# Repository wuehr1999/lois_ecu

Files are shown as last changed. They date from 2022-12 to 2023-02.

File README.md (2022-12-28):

# lois_ecu
This repository contains the [hardware](https://github.com/wuehr1999/lois_ecu/tree/main/hw), [firmware](https://github.com/wuehr1999/lois_ecu/tree/main/firmware) and [tooling](https://github.com/wuehr1999/lois_ecu/tree/main/rpmctrl_tuning) for a general purpose control unit for differential drive based wheeled robotics platforms. An image of the real hardware and a component diagram are shown below.
<p align="center">
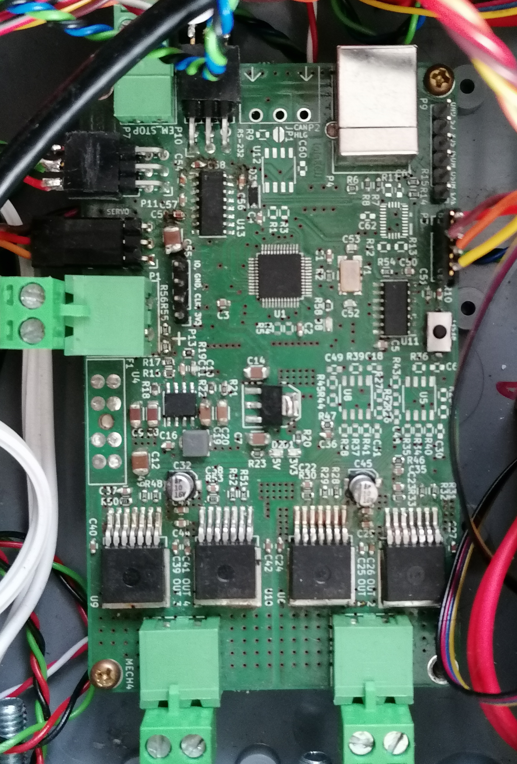
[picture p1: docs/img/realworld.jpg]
  
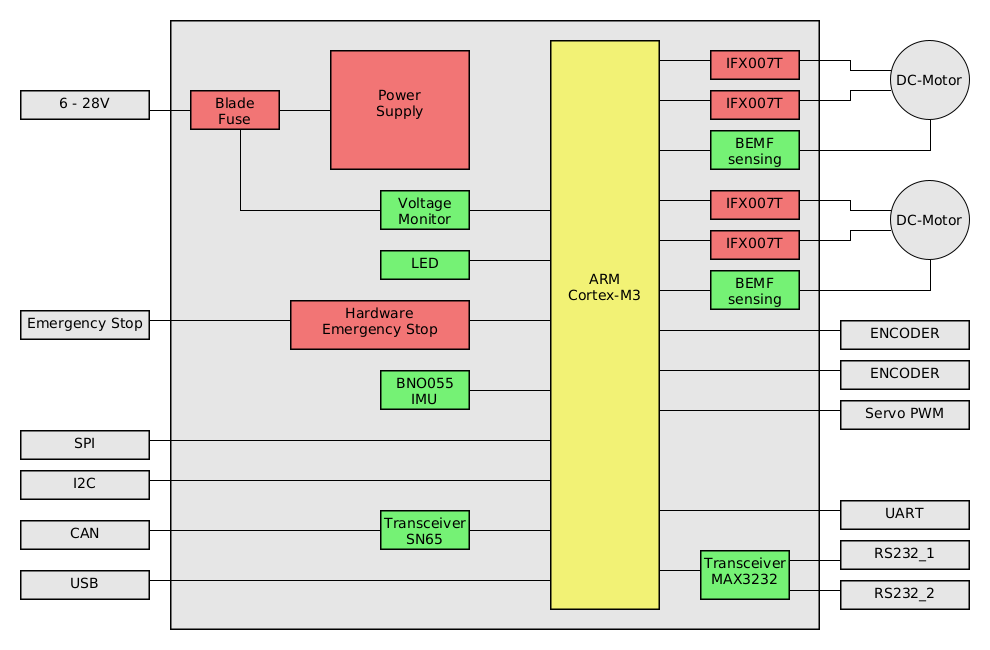
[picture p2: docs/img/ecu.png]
  
</p>

## Firmware

The [firmware](https://github.com/wuehr1999/lois_ecu/tree/main/firmware/loisECU) comes as a STM32 CubeIDE project and currently implements the following features:

- Closed single loop RPM-control for two DC-motors with encoders
- Realtime calculation of differential drive odometry
- Servo sweep for the [ball distribution device](https://github.com/generationmake/BDD)
- NMEA parser on RS232_1 (used for UBLOX GPS)
- NMEA parser on RS232_2 (used for KVH-C100 fluxgate compass)
- Host communication via UART
- 2048 Byte reealtime reord buffer ( recording of RPM, torque and compass heading over a given time )
- Easy human readable and debuggable ASCII communication leaned on modbus protocol with optional checksum

### Host communication protocol

The communication protocol is ASCII-based and the messages have the following format:

```:<8-bit command><32-bit payload><8-bit crc><\n>```

All values are written in hexadecimal, so that every message has a fixed length of 14 characters. There is also a [ROS2 driver](https://github.com/wuehr1999/lois_ecu_ros), which uses the given protocol to make the functionalities available via ROS.

The table below shows the currently implemented messages. There are also some periodic messages from the ECU to the Host. By writing the commands of this messages to the ECU, the period can be changed. The payload is then interpreted as an ```uint16``` containing the period time in milliseconds. ```0xfffe``` then means requesting a periodic message once and ```0xffff``` turns the message off completely.

| Command | Function | To ECU (E)/ To Host (H) | Payload interpretation | Periodic |
| - | - | - | - | - |
| ```0x01``` | Dutycycle of left and right motor, RPM controller gets disabled | E | ```2 x int16``` ( -100 % - 100 %)  | |
| ```0x02``` | RPM of left and right motor, RPM controller gets enabled | E | ```2 x int16``` | |
| ```0x03```  | Turn board LED on or off | E | ```bool``` | |
| ```0x04``` | Record a given amount of RPM samples | E / H | ```2 x uint16``` ( m samples left and n right ) to ECU or sequential max(m, n) ``` 2 x uint16``` ( tick timestamps in 100 ns followed by ```0x00000000``` ) to Host |  |
| ```0x05``` | Emergency stop button pressed | H | ```bool``` |  |
| ```0x06``` | Kp left controller | E | ```float32``` |  |
| ```0x07``` | Tn left controller | E | ```float32``` |  |
| ```0x08``` | Td left controller | E | ```float32``` |  |
| ```0x09``` | Kp right controller | E | ```float32``` |  |
| ```0x0a``` | Tn right controller | E | ```float32``` |  |
| ```0x0b``` | Td right controller | E | ```float32``` |  |
| ```0x0c``` | Record a given amount of compass heading samples | E | ```uint32```  n samples to ECU or sequential n + 1 ```2 x int16``` ( heading data in degrees ) followed by ```0x016A016A``` to Host |  |
| ```0x0d``` | GPS position | E / H | 3 sequential ```uint32, 2 x float32``` ( ```0xffffffff```, latitude, longitude ) | x |
| ```0x0e``` | GPS time | E / H | ```3 x uint8``` ( hours, minutes, seconds ) | x |
| ```0x0f``` | GPS date | E / H | ```3 x uint8``` ( year, month, day ) | x |
| ```0x10``` | Compass heading | E / H | ```1 x int16``` ( degrees to north ) | x |
| ```0x11``` | Terminal mode ( forward serial sensor Rx input on this interface ) | E | ```uint8``` ( Host protocol, GPS sensor, compass sensor ) | |
| ```0x12``` | Encoder overall ticks | E / H | 4 sequential ```4 x uint32``` ( ```0xffffffff```, timestamp in nanoseconds, left encoder, right encoder )  | x |
| ```0x13``` | Left encoder short level time correction | E | ```float32``` |  |
| ```0x14``` | Left encoder long level time correction | E | ```float32``` |  |
| ```0x15``` | Right encoder short level time correction | E | ```float32``` |  |
| ```0x16``` | Right encoder long level time correction | E | ```float32``` |  |
| ```0x17``` | Record a given amount of Torque samples | E / H | ```2 x uint16``` ( m samples left and n right ) to ECU or sequential max(m, n) ``` 2 x uint16``` ( torque 12-bit ADC values followed by ```0x00000000``` ) to Host |  |
| ```0x18``` | Reset all controllers, interfaces and counters | E  | - |  |
| ```0x19``` | Use ball distribution device once | E | - |  |
| ```0x20``` | Odometry calculated on robot | E / H | sequential 7 started with ```0xffffffff``` followed by ```6 x float32``` ( x, y, phi, dx, dy, dphi ) | x |

## Encoder and RPM controller tuning

There is [tooling in Scilab](https://github.com/wuehr1999/lois_ecu/tree/main/rpmctrl_tuning) provided, that can be used to find the parameters for the implemented RPM controller. The first step is recording a step response with full torque/ dutycycle and data of free spinning wheels at a constant dutycycle and  saving the data as ```*.csv``` files. This can for instance be done by using the ROS ecosystem of lois. There are also some examples in the controller tuning folder.

### Encoder correction

The ECU determines the RPM values of the robot by measuring the time of high and low levels of the encoder signals. With this implementation, also encoders with fewer steps ( usually mounted directly on the wheel ) can be used with a sufficient resolution. The problem is, that some encoders have inequal high and low times. Therefore [correction factors](https://github.com/wuehr1999/lois_ecu/blob/main/rpmctrl_tuning/edgecorrect/correct.sce) can be calculated and entered at runtime ( commands ```0x13 - 0x16``` ) from the free spinning record.

### Finding the controller parameters

The controller is updated in the ECU with a frequency of ```5 Hz```. It is only a single loop RPM controller without a cascade for torque control, as it is not necessary for most differential drivetrain applications.

There is one band limited PI controller for each motor with the transfer function ```G(s) = Kp * ( 1 + s * Tn ) / ( s * Tn * ( 1 + s * Td ))```.

The Scilab tooling helps to [approximate the plant from the step response as 1st or 2nd order system and find sufficient controller settings](https://github.com/wuehr1999/lois_ecu/blob/main/rpmctrl_tuning/stepresponse/main.sce). The tuning paradigm is the compensation of the most critical pole of the plant followed by gain optimization. The following [goal parameters](https://github.com/wuehr1999/lois_ecu/blob/main/rpmctrl_tuning/stepresponse/init.sce) that can be selected:
- Encoder steps per revolution
- Controller frequency in Hz
- Don't optimize for phase margin with gain optimum ( ```Td = 0``` )
- Maximum overshoot inpercent
- Step response destination in % for optimization ( average RPM value during operation )
- Stabilization time in seconds
- Tolerance band in %

## PCB toplayer

<p align="center">
  <img src=docs/img/toplayer.png width="75%">
</p>

## PCB bottomlayer

<p align="center">
  <img src=docs/img/bottomlayer.png width="75%">
</p>

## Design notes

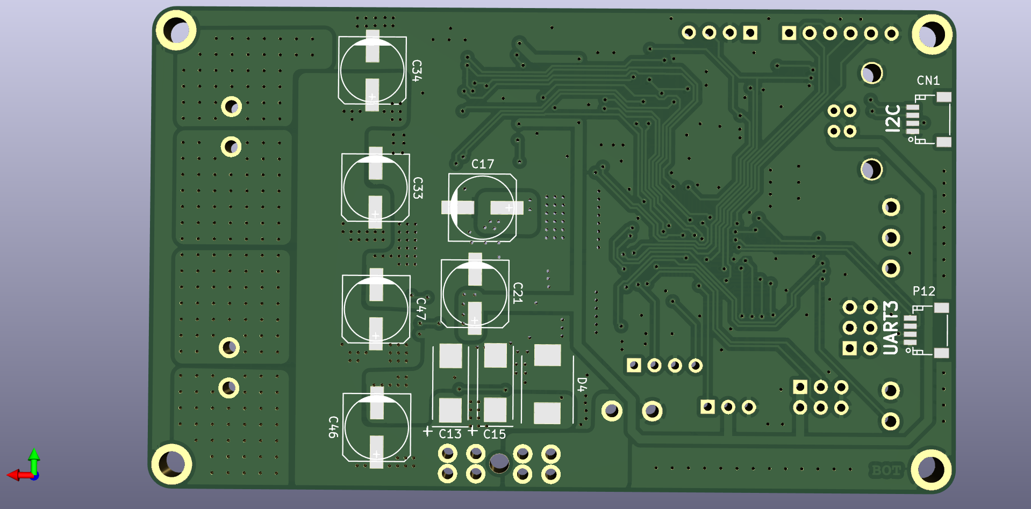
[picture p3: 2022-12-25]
docs/img/bottomlayer.png

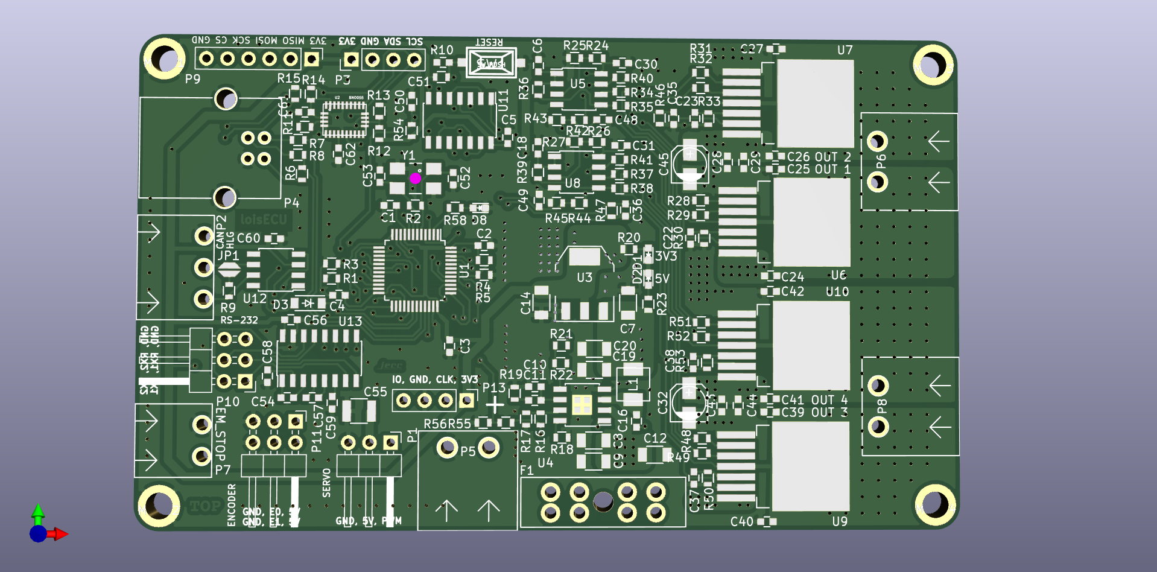
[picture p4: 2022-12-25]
docs/img/toplayer.png

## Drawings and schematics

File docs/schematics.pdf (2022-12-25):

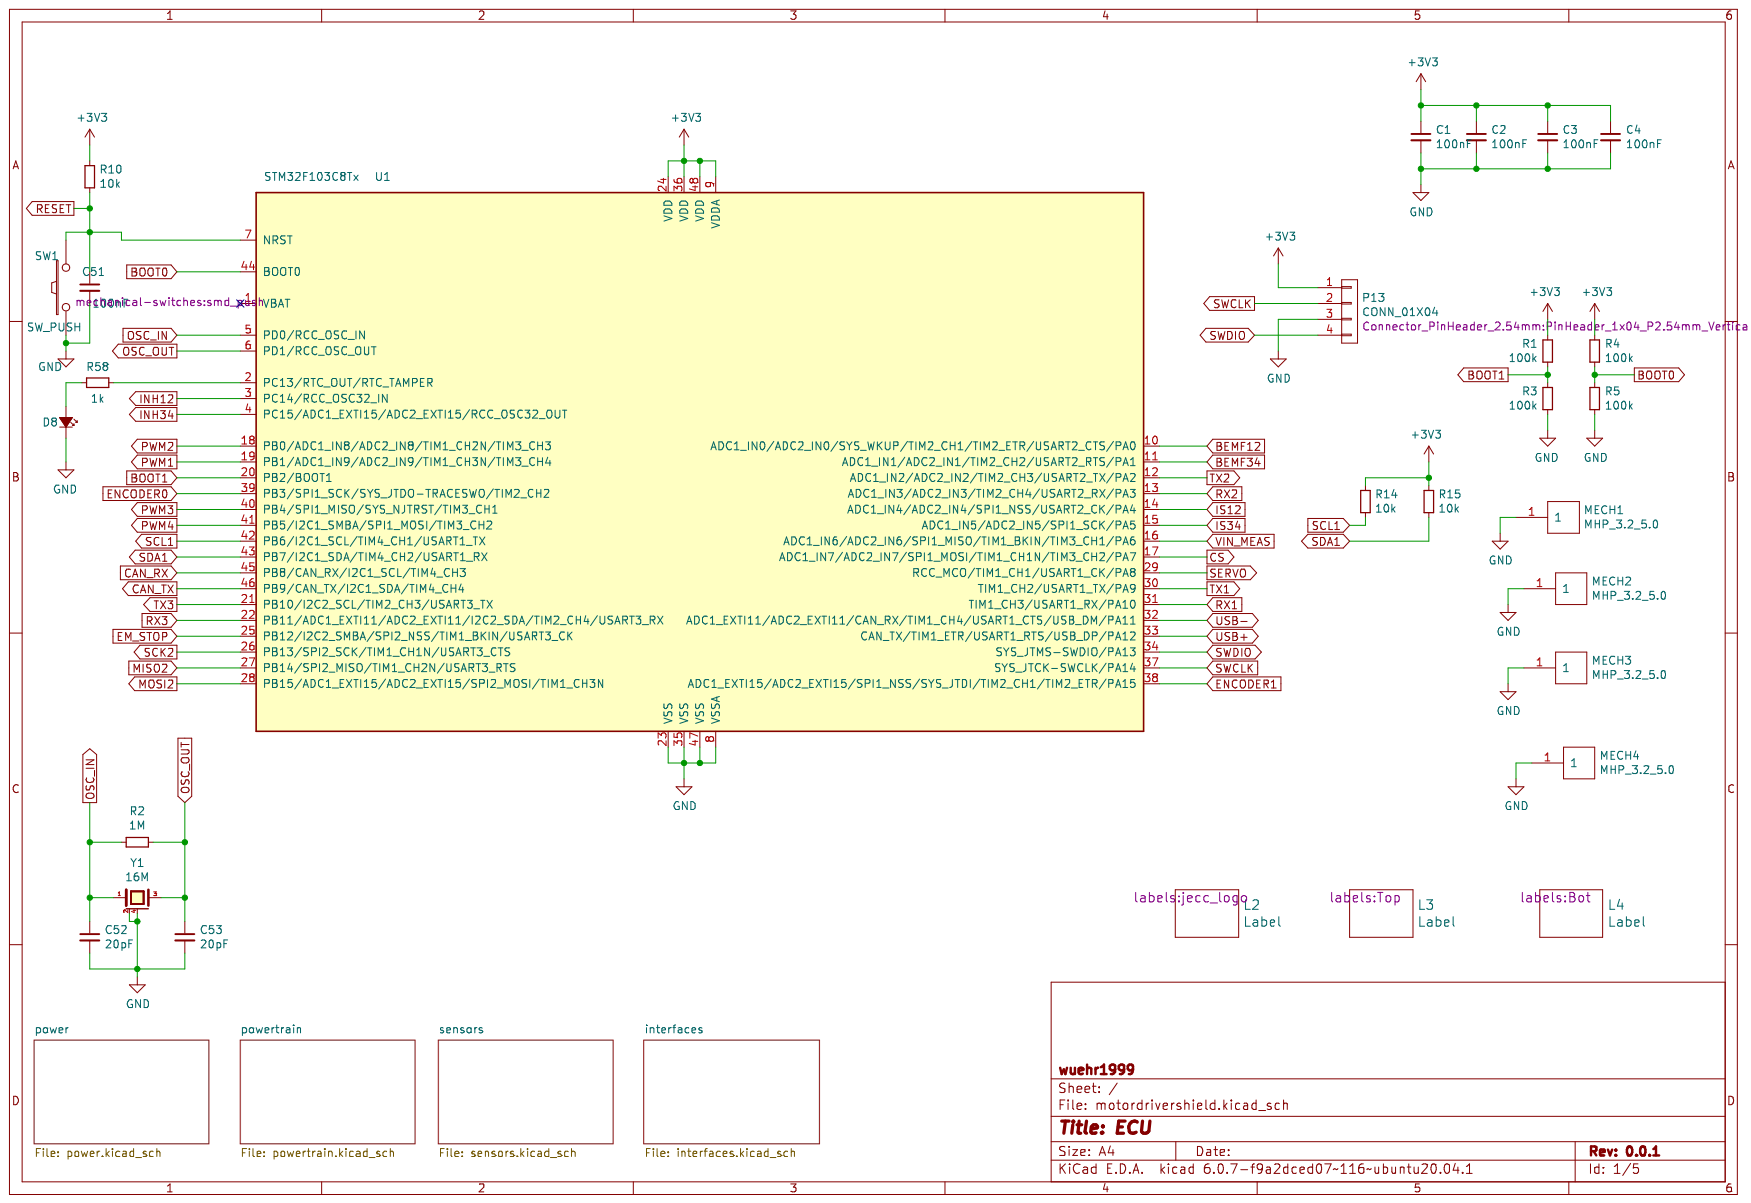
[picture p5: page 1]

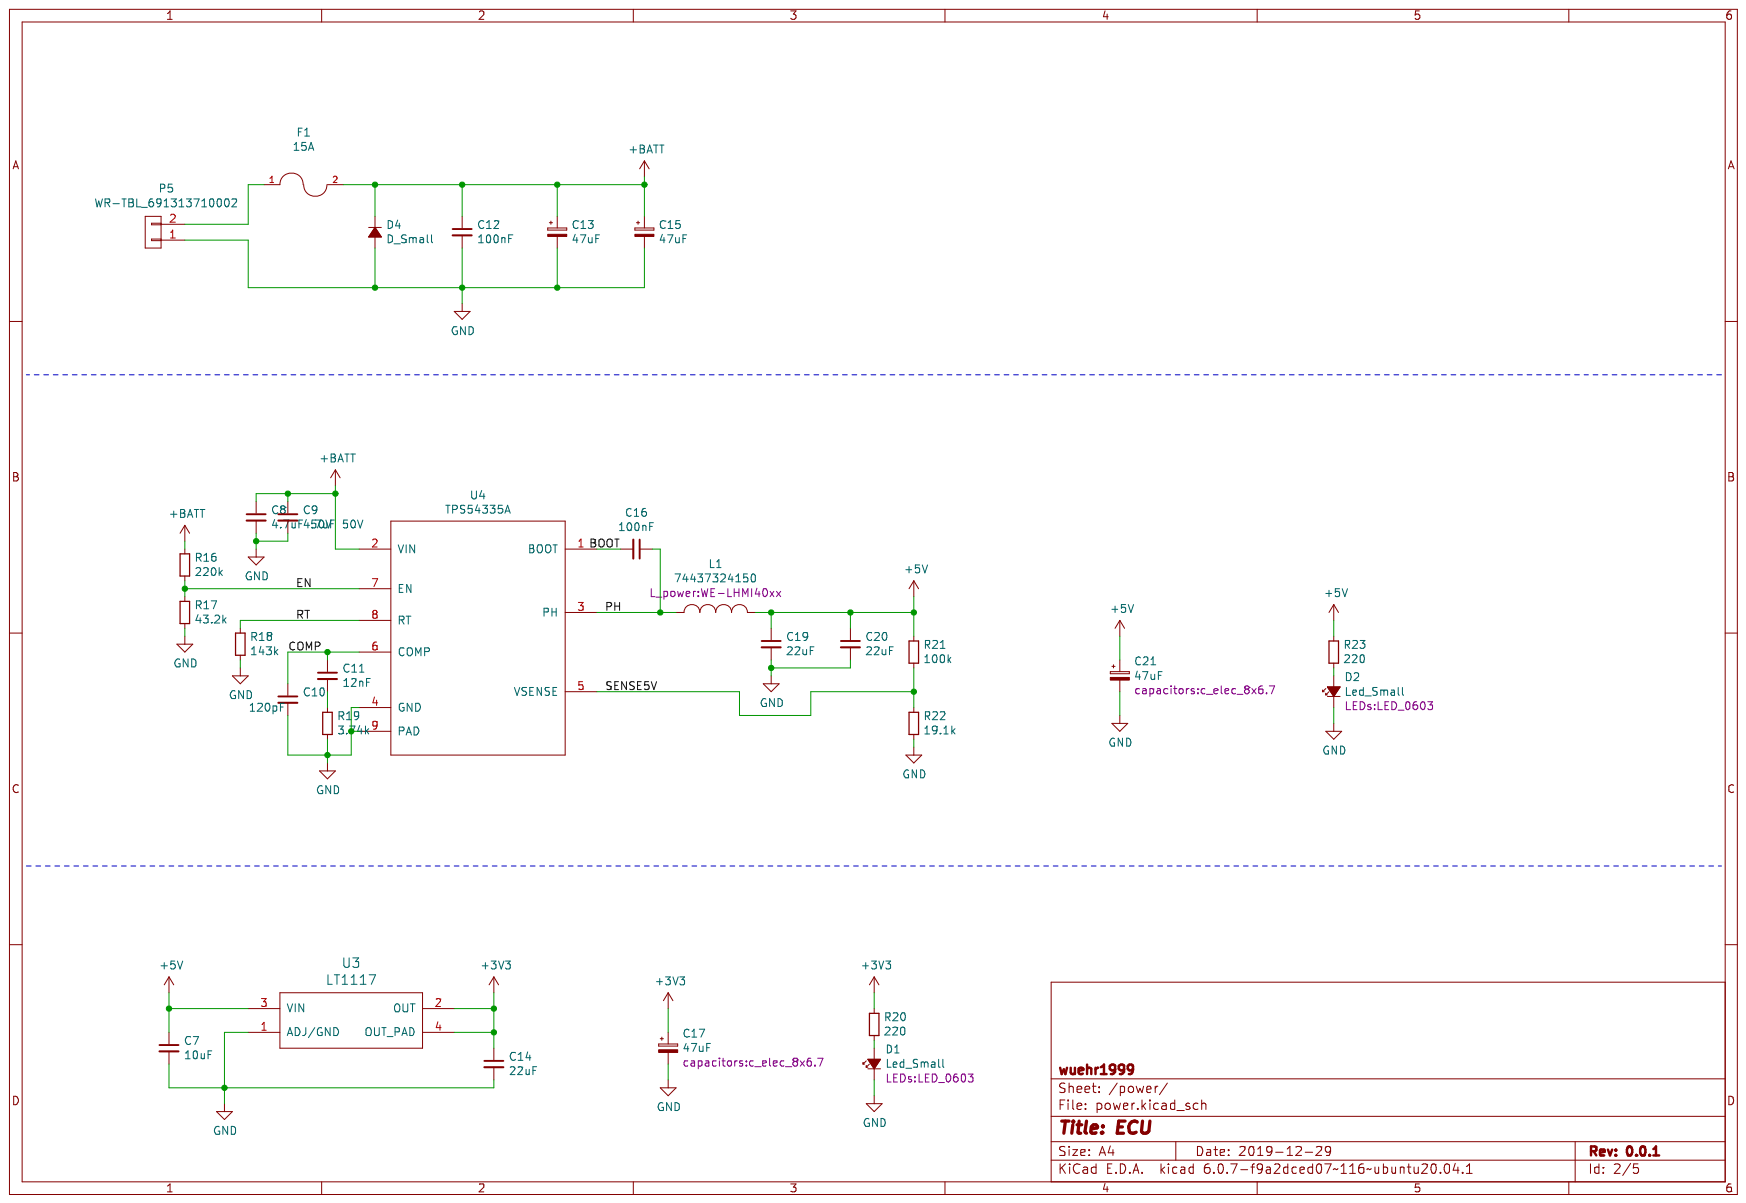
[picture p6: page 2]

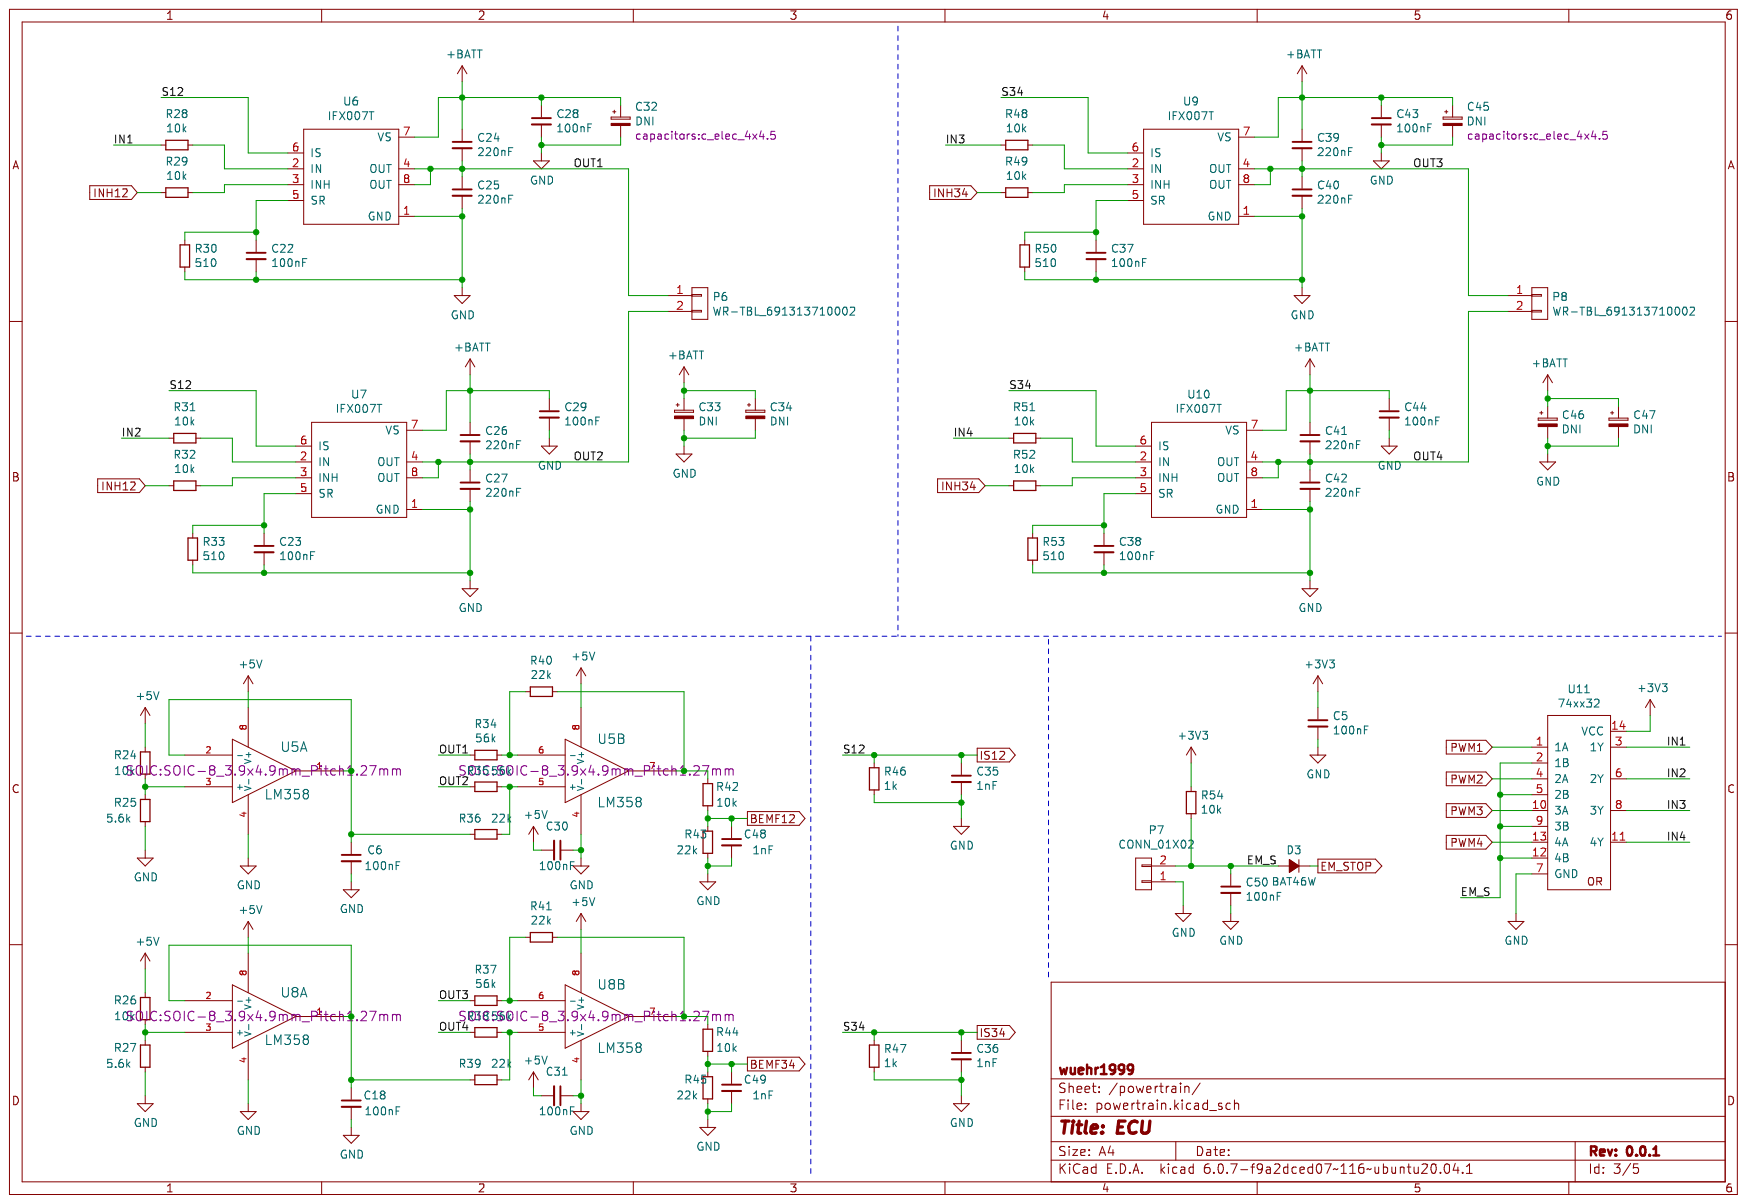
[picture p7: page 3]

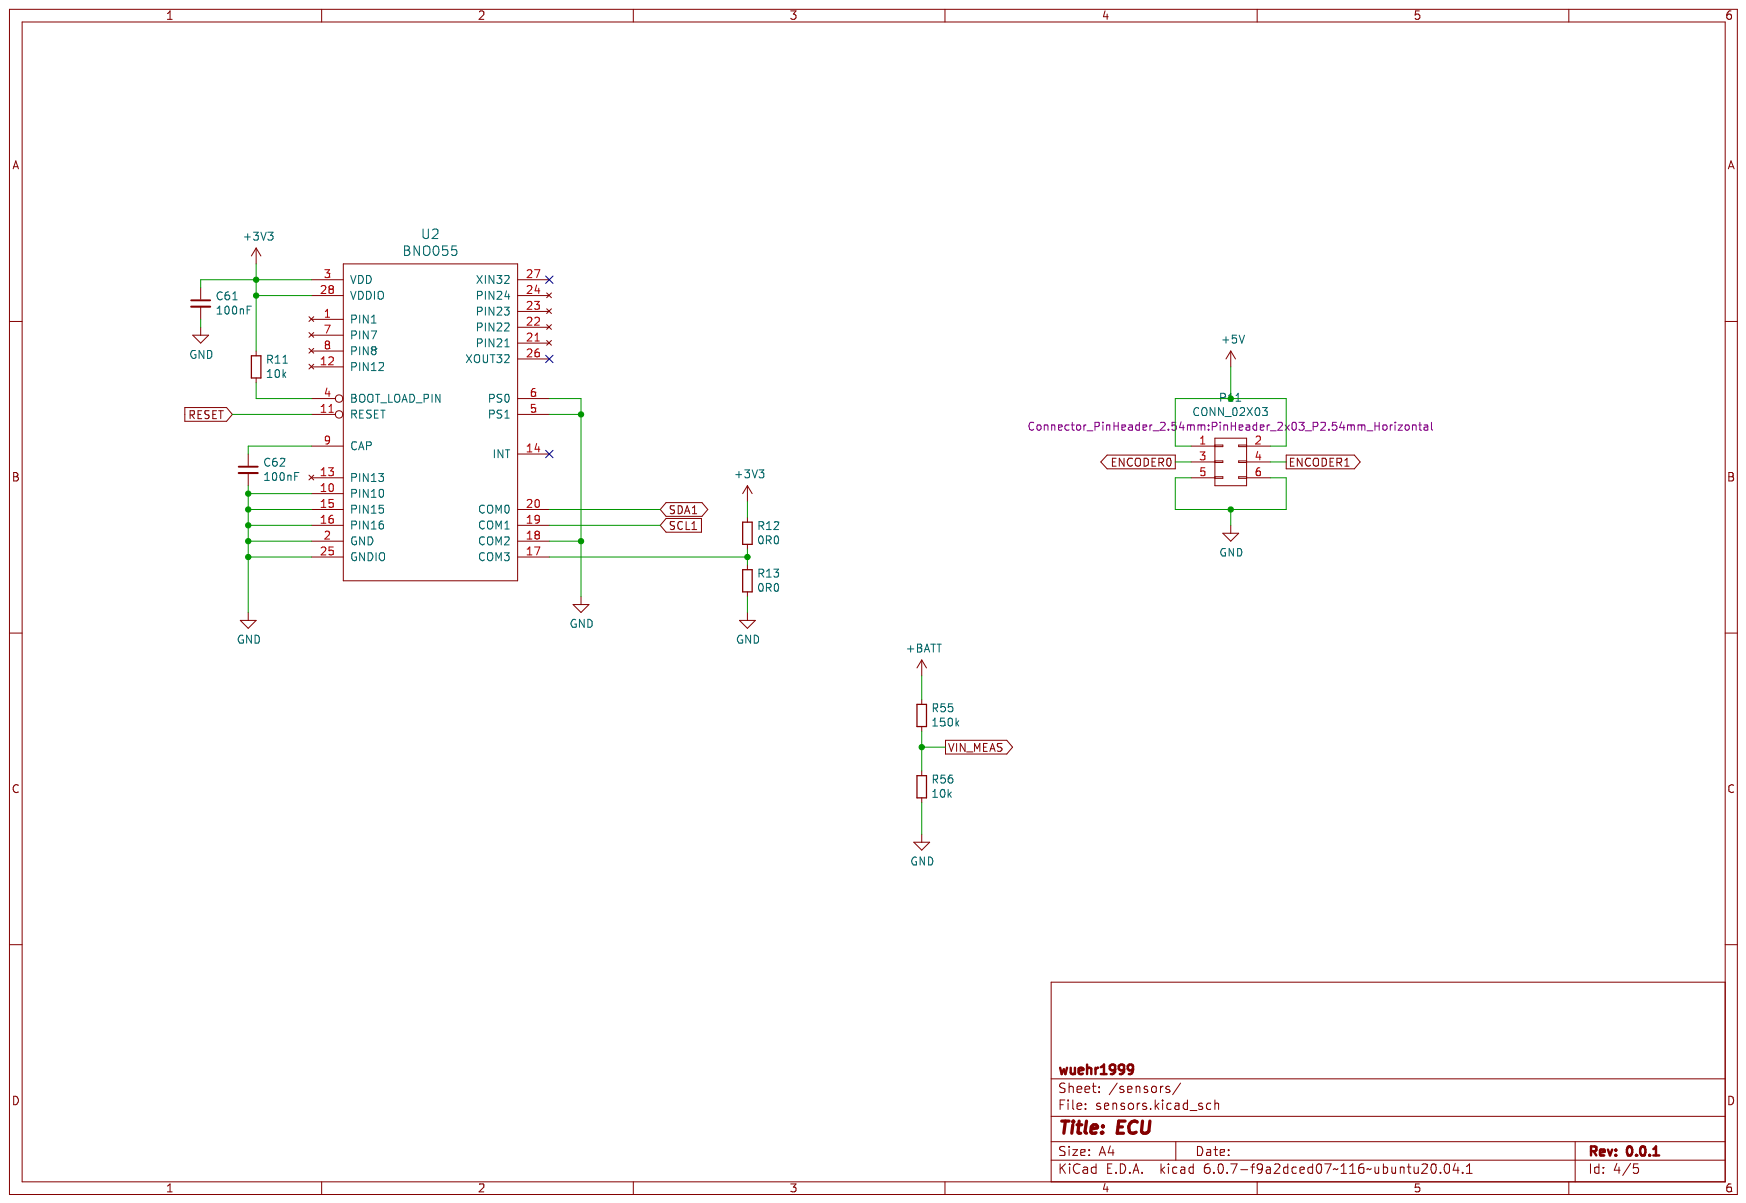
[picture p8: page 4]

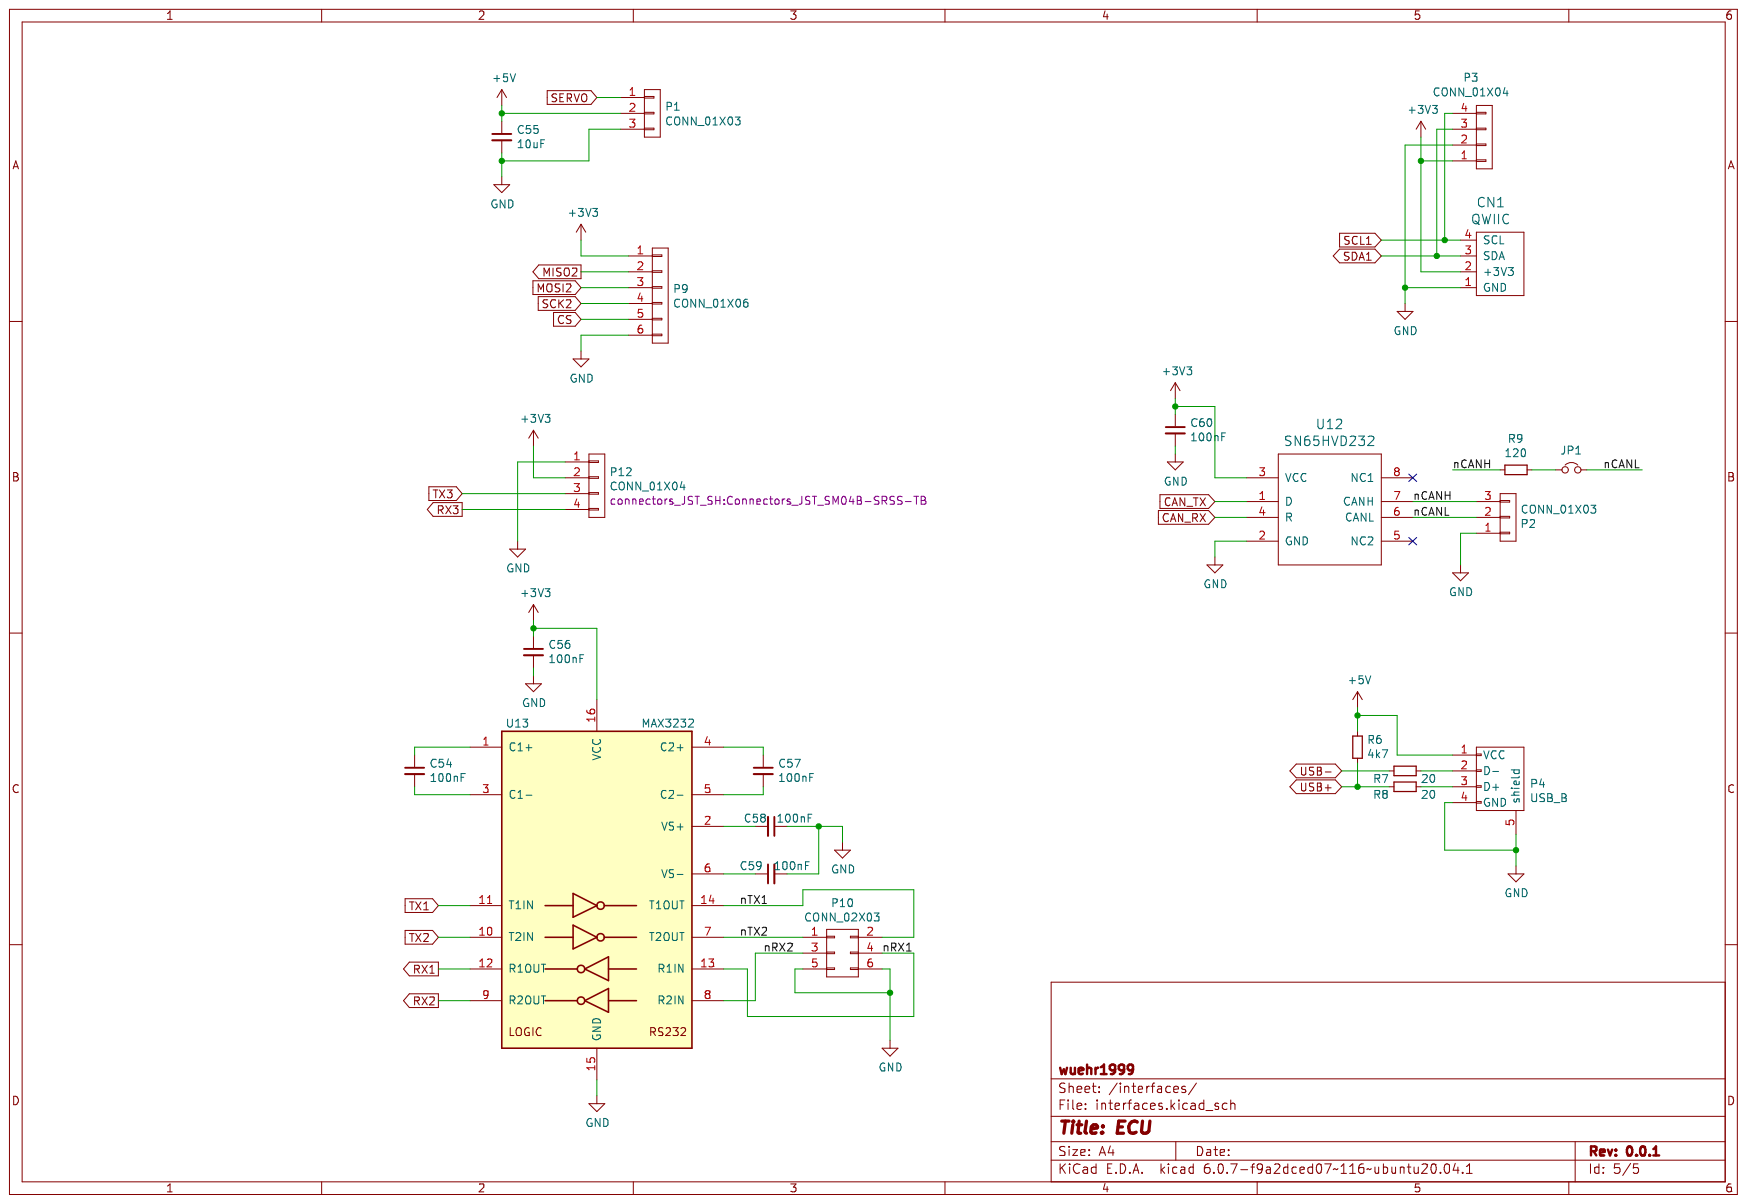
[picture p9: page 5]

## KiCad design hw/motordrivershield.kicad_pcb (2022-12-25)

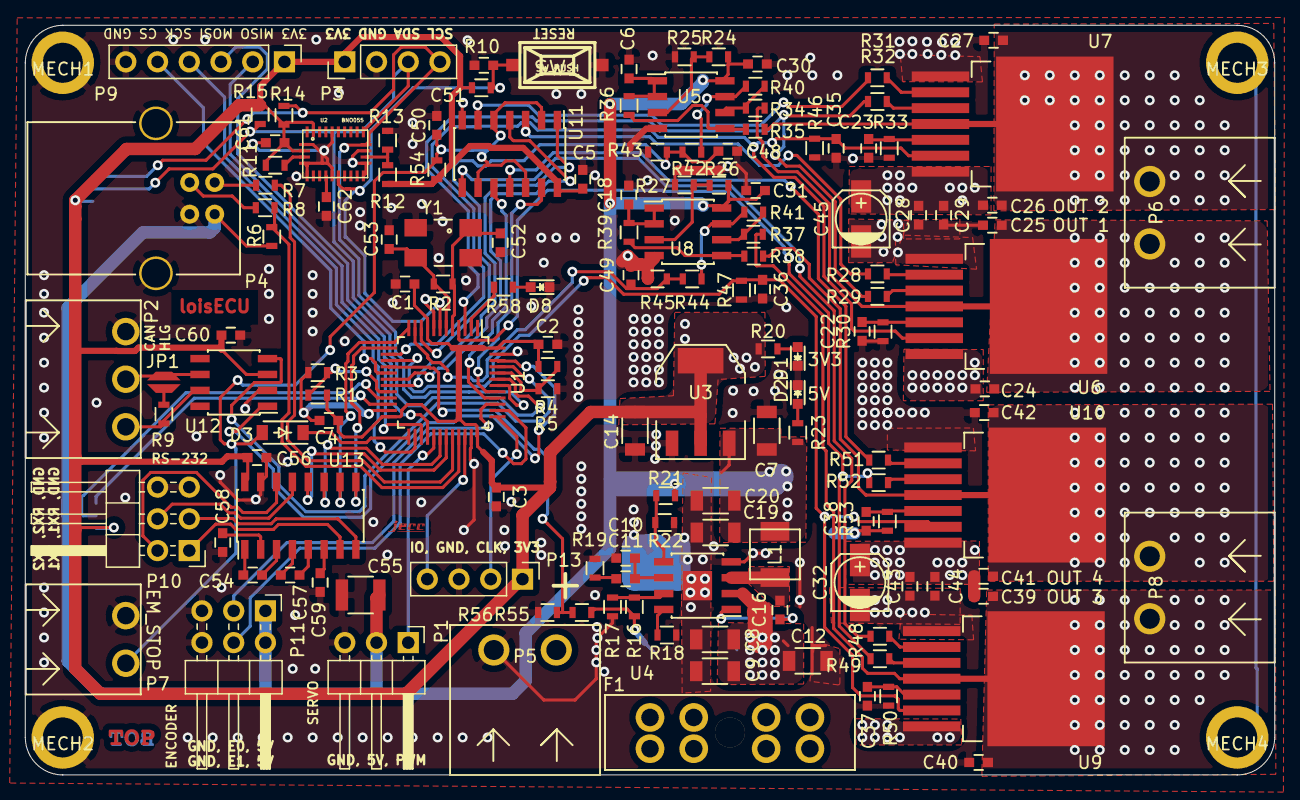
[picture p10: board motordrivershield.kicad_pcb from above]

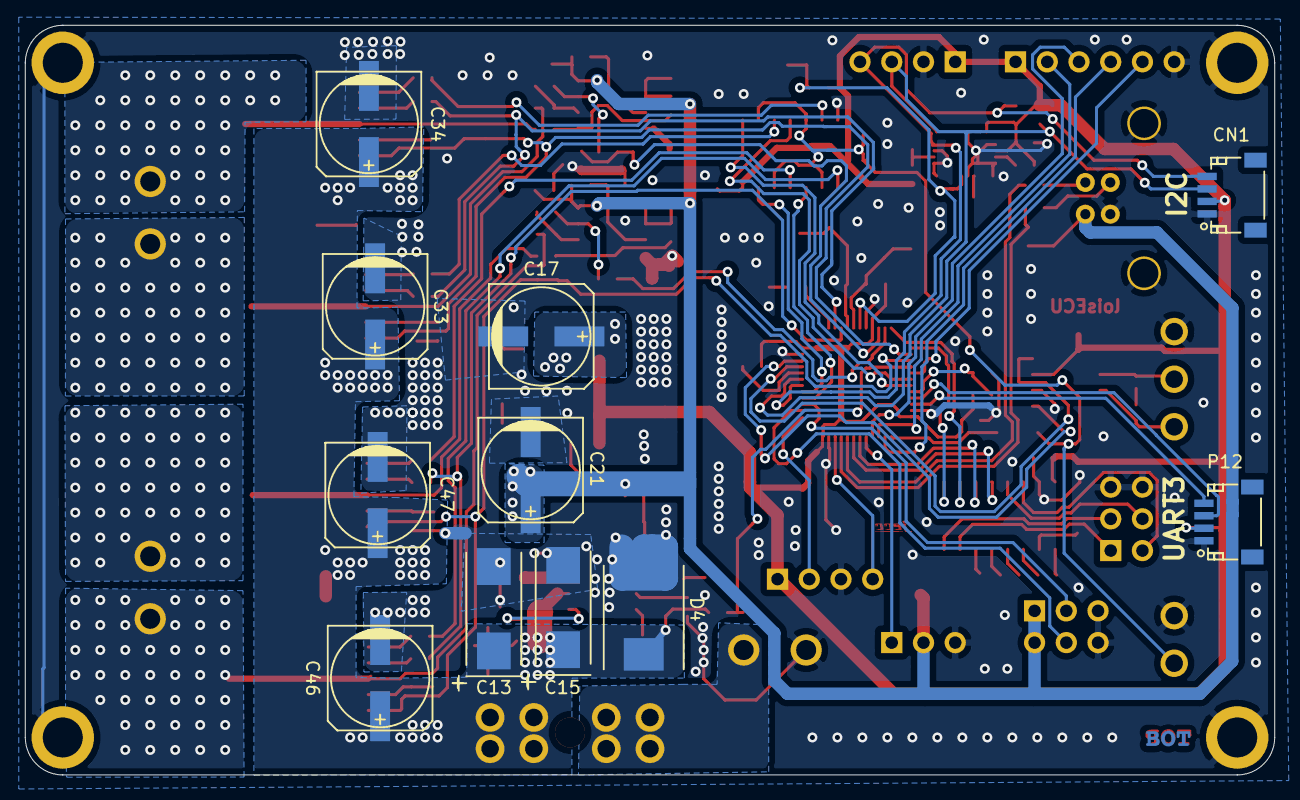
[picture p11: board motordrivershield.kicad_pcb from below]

Board: 2 copper layers, 100.0 x 60.0 mm, 163 parts (11 on the bottom side), 103 nets.

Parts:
C1, C2, C3, C4, C5, C6, C16, C18, C22, C23, C28, C29, C30, C31, C37, C38, C43, C44, C50, C51, C54, C56, C57, C58, C59, C60, C61, C62: 100nF; C_0603
C7: 10uF; C_1206
C8, C9: 4.7uF 50V; C_1206
C10: 120pF; C_0603
C11: 12nF; C_0603
C12: 100nF; C_1206
C13, C15: 47uF; TantalC_SizeD_EIA-7343_Wave
C14, C19, C20: 22uF; C_1206
C17, C21: 47uF; c_elec_8x6.7
C24, C25, C26, C27, C39, C40, C41, C42: 220nF; C_0603
C32, C45: DNI; c_elec_4x4.5
C33, C34, C46, C47: DNI; c_elec_8x6.7
C35, C36, C48, C49: 1nF; C_0603
C52, C53: 20pF; C_0603
C55: 10uF; C_1210
CN1: QWIIC; Connectors_JST_SM04B-SRSS-TB
D1, D2, D8: Led_Small; LED_0603
D3: BAT46W; SOD-123
D4: D_Small; DO-214AB
F1: 15A; Fuseholder_ATO_Blade_littlefuse_8_Pin
JP1: Jumper_NC_Small; SolderJumper_2mm
L1: 74437324150; WE-LHMI40xx
L2: Label; jecc_logo
L3: Label; Top
L4: Label; Bot
MECH1, MECH2, MECH3, MECH4: MHP_3.2_5.0
P1: CONN_01X03; PinHeader_1x03_P2.54mm_Horizontal
P2: CONN_01X03; WR-TBL_691322310003
P3, P13: CONN_01X04; PinHeader_1x04_P2.54mm_Vertical
P4: USB_B
P5, P6, P8: WR-TBL_691313710002
P7: CONN_01X02; WR-TBL_691322310002
P9: CONN_01X06; PinHeader_1x06_P2.54mm_Vertical
P10, P11: CONN_02X03; PinHeader_2x03_P2.54mm_Horizontal
P12: CONN_01X04; Connectors_JST_SM04B-SRSS-TB
R1, R3, R4, R5, R21: 100k; R_0603
R2: 1M; R_0603
R6: 4k7; R_0603
R7, R8: 20; R_0603
R9: 120; R_0603
R10, R11, R14, R15, R24, R26, R28, R29, R31, R32, R42, R44, R48, R49, R51, R52, R54, R56: 10k; R_0603
R12, R13: 0R0; R_0603
R16: 220k; R_0603
R17: 43.2k; R_0603
R18: 143k; R_0603
R19: 3.74k; R_0603
R20, R23: 220; R_0603
R22: 19.1k; R_0603
R25, R27: 5.6k; R_0603
R30, R33, R50, R53: 510; R_0603
R34, R35, R37, R38: 56k; R_0603
R36, R39, R40, R41, R43, R45: 22k; R_0603
R46, R47, R58: 1k; R_0603
R55: 150k; R_0603
SW1: SW_PUSH; smd_push
U1: STM32F103C8Tx; LQFP-48_7x7mm_Pitch0.5mm
U2: BNO055; LGA-28-5832
U3: LT1117; SOT-223
U4: TPS54335A; SOIC-8-1EP_3.9x4.9mm_Pitch1.27mm
U5, U8: LM358; SOIC-8_3.9x4.9mm_Pitch1.27mm
U6, U7, U9, U10: IFX007T; TO-263-7Lead
U11: 74xx32; SOIC-14_3.9x8.7mm_Pitch1.27mm
U12: SN65HVD232; SOIC-8_3.9x4.9mm_Pitch1.27mm
U13: MAX3232; SOIC-16_3.9x9.9mm_Pitch1.27mm
Y1: 16M; Crystal_SMD_0603_4Pads

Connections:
+3V3: C1.1, C2.1, C3.1, C4.1, C5.1, C14.1, C17.1, C56.1, C60.1, C61.1, CN1.2, P3.1, P9.1, P12.2, P13.1, R1.1, R4.1, R10.1, R11.1, R12.1, R14.1, R15.1, R20.1, R54.1, U1.9, U1.24, U1.36, U1.48, U2.3, U2.28, U3.2, U3.4, U11.14, U12.3, U13.16
+5V: C7.1, C19.1, C20.1, C21.1, C30.2, C31.2, C55.1, L1.2, P1.2, P4.1, P11.1, P11.2, R6.1, R21.1, R23.1, R24.1, R26.1, U3.3, U5.8, U8.8
+BATT: C8.1, C9.1, C12.1, C13.1, C15.1, C24.1, C26.1, C28.1, C29.1, C32.1, C33.1, C34.1, C39.1, C41.1, C43.1, C44.1, C45.1, C46.1, C47.1, D4.1, F1.2, R16.1, R55.1, U4.2, U6.7, U7.7, U9.7, U10.7
/interfaces/nCANH: P2.3, R9.2, U12.7
/interfaces/nCANL: JP1.2, P2.2, U12.6
/interfaces/nRX1: P10.4, U13.13
/interfaces/nRX2: P10.3, U13.8
/interfaces/nTX1: P10.2, U13.14
/interfaces/nTX2: P10.1, U13.7
/power/COMP: C10.1, C11.1, U4.6
/power/EN: R16.2, R17.1, U4.7
/power/PH: C16.1, L1.1, U4.3
/power/RT: R18.1, U4.8
/power/SENSE5V: R21.2, R22.1, U4.5
/powertrain/EM_S: C50.1, D3.2, P7.2, R54.2, U11.2, U11.5, U11.9, U11.12
/powertrain/IN1: R28.2, U11.3
/powertrain/IN2: R31.2, U11.6
/powertrain/IN3: R48.2, U11.8
/powertrain/IN4: R51.2, U11.11
/powertrain/OUT1: C24.2, C25.1, P6.1, R34.2, U6.4, U6.8
/powertrain/OUT2: C26.2, C27.1, P6.2, R35.2, U7.4, U7.8
/powertrain/OUT3: C39.2, C40.1, P8.1, R37.2, U9.4, U9.8
/powertrain/OUT4: C41.2, C42.1, P8.2, R38.2, U10.4, U10.8
BEMF12: C48.1, R42.2, R43.1, U1.10
BEMF34: C49.1, R44.2, R45.1, U1.11
BOOT0: R4.2, R5.1, U1.44
BOOT1: R1.2, R3.1, U1.20
CAN_RX: U1.45, U12.4
CAN_TX: U1.46, U12.1
CS: P9.5, U1.17
EM_STOP: D3.1, U1.25
ENCODER0: P11.3, U1.39
ENCODER1: P11.4, U1.38
GND: C1.2, C2.2, C3.2, C4.2, C5.2, C6.2, C7.2, C8.2, C9.2, C10.2, C12.2, C13.2, C14.2, C15.2, C17.2, C18.2, C19.2, C20.2, C21.2, C22.2, C23.2, C25.2, C27.2, C28.2, C29.2, C30.1, C31.1, C32.2, C33.2, C34.2, C35.2, C36.2, C37.2, C38.2, C40.2, C42.2, C43.2, C44.2, C45.2, C46.2, C47.2, C48.2, C49.2, C50.2, C51.2, C52.2, C53.2, C55.2, C56.2, C58.1, C59.2, C60.2, C61.2, C62.2, CN1.1, D1.1, D2.1, D4.2, D8.1, MECH1.1, MECH2.1, MECH3.1, MECH4.1, P1.3, P2.1, P3.2, P4.4, P4.5, P5.1, P7.1, P9.6, P10.5, P10.6, P11.5, P11.6, P12.1, P13.3, R3.2, R5.2, R13.2, R17.2, R18.2, R19.2, R22.2, R25.2, R27.2, R30.2, R33.2, R43.2, R45.2, R46.2, R47.2, R50.2, R53.2, R56.2, SW1.2, U1.8, U1.23, U1.35, U1.47, U2.2, U2.5, U2.6, U2.10, U2.15, U2.16, U2.18, U2.25, U3.1, U4.4, U4.9, U5.4, U6.1, U7.1, U8.4, U9.1, U10.1, U11.7, U12.2, U13.15, Y1.2, Y1.4
INH12: R29.2, R32.2, U1.3
INH34: R49.2, R52.2, U1.4
IS12: C35.1, R46.1, U1.14, U6.6, U7.6
IS34: C36.1, R47.1, U1.15, U9.6, U10.6
MISO2: P9.2, U1.27
MOSI2: P9.3, U1.28
unnamed: C6.1, R36.2, U5.1, U5.2
unnamed: C11.2, R19.1
unnamed: C16.2, U4.1
unnamed: C18.1, R39.2, U8.1, U8.2
unnamed: C22.1, R30.1, U6.5
unnamed: C23.1, R33.1, U7.5
unnamed: C37.1, R50.1, U9.5
unnamed: C38.1, R53.1, U10.5
unnamed: C54.1, U13.1
unnamed: C54.2, U13.3
unnamed: C57.1, U13.4
unnamed: C57.2, U13.5
unnamed: C58.2, U13.2
unnamed: C59.1, U13.6
unnamed: C62.1, U2.9
unnamed: D1.2, R20.2
unnamed: D2.2, R23.2
unnamed: D8.2, R58.1
unnamed: F1.1, P5.2
unnamed: JP1.1, R9.1
unnamed: P4.2, R7.1
unnamed: P4.3, R8.1
unnamed: R11.2, U2.4
unnamed: R12.2, R13.1, U2.17
unnamed: R24.2, R25.1, U5.3
unnamed: R26.2, R27.1, U8.3
unnamed: R28.1, U6.2
unnamed: R29.1, U6.3
unnamed: R31.1, U7.2
unnamed: R32.1, U7.3
unnamed: R34.1, R40.2, U5.6
unnamed: R35.1, R36.1, U5.5
unnamed: R37.1, R41.2, U8.6
unnamed: R38.1, R39.1, U8.5
unnamed: R40.1, R42.1, U5.7
unnamed: R41.1, R44.1, U8.7
unnamed: R48.1, U9.2
unnamed: R49.1, U9.3
unnamed: R51.1, U10.2
unnamed: R52.1, U10.3
unnamed: R58.2, U1.2
OSC_IN: C52.1, R2.2, U1.5, Y1.1
OSC_OUT: C53.1, R2.1, U1.6, Y1.3
PWM1: U1.19, U11.1
PWM2: U1.18, U11.4
PWM3: U1.40, U11.10
PWM4: U1.41, U11.13
RESET: C51.1, R10.2, SW1.1, U1.7, U2.11
RX1: U1.31, U13.12
RX2: U1.13, U13.9
RX3: P12.4, U1.22
SCK2: P9.4, U1.26
SCL1: CN1.4, P3.4, R14.2, U1.42, U2.19
SDA1: CN1.3, P3.3, R15.2, U1.43, U2.20
SERVO: P1.1, U1.29
SWCLK: P13.2, U1.37
SWDIO: P13.4, U1.34
TX1: U1.30, U13.11
TX2: U1.12, U13.10
TX3: P12.3, U1.21
USB+: R6.2, R8.2, U1.33
USB-: R7.2, U1.32
VIN_MEAS: R55.2, R56.1, U1.16

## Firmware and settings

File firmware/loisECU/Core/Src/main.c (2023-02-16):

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

/* Includes ------------------------------------------------------------------*/
#include "main.h"

/* USER CODE BEGIN PD */
#define SERVO_OFFSET 1750
#define SERVO_RANGE 6500
#define BALLSHITTER_TIME 2000
/* USER CODE END PD */

ADC_HandleTypeDef hadc1;
DMA_HandleTypeDef hdma_adc1;

TIM_HandleTypeDef htim1;
TIM_HandleTypeDef htim2;
TIM_HandleTypeDef htim3;
TIM_HandleTypeDef htim4;

UART_HandleTypeDef huart1;
UART_HandleTypeDef huart2;
UART_HandleTypeDef huart3;

/* USER CODE BEGIN PV */
// Host communication interface
char interfaceBuf[MEMDEPTH_INTERFACE];
QUEUE_t interfaceQueue;
INTERFACE_Data_t interfaceData;

// RPM control and odometry
ODOMETRY_t odom;
RPMCTRL_t ctrlLeft, ctrlRight;
CTRL_t piLeft, piRight;

// Software I2C
uint8_t wireRx[MEMDEPTH_WIRE];
uint8_t wireTx[MEMDEPTH_WIRE];
QUEUE_t wireRxQueue, wireTxQueue;
WIRE_t wire;

// UART input
char uart3In, uart1In, uart2In;

// Recording
char recordBuf1[MEMDEPTH_RECORD];
char recordBuf2[MEMDEPTH_RECORD];
QUEUE_t record1, record2;
Recordmode recordmode = RECORD_RPM;
bool recordDone = false;
uint32_t records = 0;
uint32_t recordIt = 0;

// Compass and GPS
char kvhBuf[MEMDEPTH_KVH];
char gpsBuf[MEMDEPTH_GPS];
QUEUE_t kvhQueue;
QUEUE_t gpsQueue;

// General data containers
NMEA_InputData_t kvhInput;
MovingAvg_t kvhFilter;
int kvhFilterBuf[MEMDEPTH_KVH_MOVINGAVG];

NMEA_InputData_t gpsInput;

GPSData_t gpsData;

uint32_t adcValues[ADC_SAMPLES];
bool tgl = false;

TERMINALMODE_t terminalMode;

EMERGENCY_t emergencyStop;
bool shit;
/* USER CODE END PV */

void SystemClock_Config(void);
static void MX_GPIO_Init(void);
static void MX_DMA_Init(void);
static void MX_ADC1_Init(void);
static void MX_TIM1_Init(void);
static void MX_TIM2_Init(void);
static void MX_TIM3_Init(void);
static void MX_TIM4_Init(void);
static void MX_USART1_UART_Init(void);
static void MX_USART2_UART_Init(void);
static void MX_USART3_UART_Init(void);
/* USER CODE BEGIN 0 */
/*
 * @brief Toggle SPI chipselect for debugging.
 */
void CSTGL()
{
	tgl = !tgl;
	if(tgl)
	{
	 HAL_GPIO_WritePin(CS_GPIO_Port, CS_Pin, 1);
	}
	else
	{
	 HAL_GPIO_WritePin(CS_GPIO_Port, CS_Pin, 0);
	}
}

/*
 * @brief Disable IRQs
 */
void disableIRQ()
{
	__disable_irq();
}

/*
 * @brief Enable IRQs and restart UART
 */
void enableIRQ()
{
	__enable_irq();
	HAL_UART_Receive_IT(&huart1, (uint8_t*)&uart1In, 1);
	HAL_UART_Receive_IT(&huart2, (uint8_t*)&uart2In, 1);
	HAL_UART_Receive_IT(&huart3, (uint8_t*)&uart3In, 1);
}

/*
 * @brief Send message to host
 * @param message Message payload
 * @prarm len Message length
 */
void INTERFACE_SendMessage(char* message, int len)
{
	if(!TERMINALMODE_IsEnabled(&terminalMode))
	{
		HAL_UART_Transmit(&huart3, (uint8_t*)message, (uint16_t)len, 1000);
	}
}

/*
 * @brief UART ISR
 * @brief Pushes data to corresponding dataqueues depending on operation mode.
 */
void HAL_UART_RxCpltCallback(UART_HandleTypeDef *huart)
{
	disableIRQ();
	if(huart->Instance == huart1.Instance) // GPS receiver
	{
		if(!QUEUE_IsFull(&gpsQueue))
		{
			QUEUE_Push(uart1In, &gpsQueue);
		}

		if(TERMINALMODE_IsEnabled(&terminalMode))
		{
			if(!QUEUE_IsFull(&record2))
			{
				QUEUE_Push(uart1In, &record2);
			}
		}
	}
	else if(huart->Instance == huart2.Instance) // Compass
	{
		if(!QUEUE_IsFull(&kvhQueue))
		{
			QUEUE_Push(uart2In, &kvhQueue);
		}

		if(TERMINALMODE_IsEnabled(&terminalMode))
		{
			if(!QUEUE_IsFull(&record2))
			{
				QUEUE_Push(uart2In, &record2);
			}
		}
	}
	else if(huart->Instance == huart3.Instance) // Host communication
	{
		if(!QUEUE_IsFull(&interfaceQueue))
		{
			QUEUE_Push(uart3In, &interfaceQueue);
		}

		if(TERMINALMODE_IsEnabled(&terminalMode))
		{
			if(!QUEUE_IsFull(&record1))
			{
				QUEUE_Push(uart3In, &record1);
			}
		}
	}
	enableIRQ();
}

/**
 * @brief Process recording activities and send data to host if demanded.
 * @brief Disables and reenables IRQs
 */
void RECORD_Process()
{
	char msgBuf[ROBOT_MESSAGE_MAXLEN];
	int len;
	int instruction;
	if(RECORD_RPM == recordmode || RECORD_CURRENT == recordmode) // RPM or Current
	{
		instruction = ROBOT_INSTRUCTION_RECORDRPM;
		if(RPMCTRL_IsRecordDone(&ctrlLeft) && RPMCTRL_IsRecordDone(&ctrlRight))
		{
			disableIRQ();
			RPMCTRL_StopRecord(&ctrlLeft);
			RPMCTRL_StopRecord(&ctrlRight);
			while(!QUEUE_IsEmpty(&record1) || !QUEUE_IsEmpty(&record2))
			{	  if(!QUEUE_IsEmpty(&kvhQueue))
			  {
				  NMEA_Parse(QUEUE_Pop(&kvhQueue), &kvhInput);
			  }
				uint16_t val1 = 10;
				uint16_t val2 = 10;
				if(!QUEUE_IsEmpty(&record1))
				{
					val1 = QUEUE_Pop16(&record1);
				}
				if(!QUEUE_IsEmpty(&record2))
				{
					val2 = QUEUE_Pop16(&record2);
				}
				len = INTERFACE_CreateMessage16(msgBuf, ROBOT_INSTRUCTION_RECORDRPM, val1, val2);
				INTERFACE_SendMessage(msgBuf, len);
			}
			len = INTERFACE_CreateMessage16(msgBuf, instruction, 0, 0);
			INTERFACE_SendMessage(msgBuf, len);
			INTERFACE_ResetPeriodics();
			enableIRQ();
		}
	}
	else if(RECORD_HEADING == recordmode && recordDone) // Compass heading
	{
		uint16_t val1 = 0;
		uint16_t val2 = 0;
		instruction = ROBOT_INSTRUCTION_RECORDHEADING;
		disableIRQ();
		while(!QUEUE_IsEmpty(&record1))
		{
			val1 = 362;
			val2 = 362;
			if(!QUEUE_IsEmpty(&record1))
			{
				val1 = QUEUE_Pop16(&record1);
			}
			if(!QUEUE_IsEmpty(&record1))
			{
				val2 = QUEUE_Pop16(&record1);
			}
			len = INTERFACE_CreateMessage16(msgBuf, instruction, val1, val2);
			INTERFACE_SendMessage(msgBuf, len);
		}
		while(!QUEUE_IsEmpty(&record2))
		{
			val1 = 362;
			val2 = 362;
			if(!QUEUE_IsEmpty(&record2))
			{
				val1 = QUEUE_Pop16(&record2);
			}
			if(!QUEUE_IsEmpty(&record2))
			{
				val2 = QUEUE_Pop16(&record2);
			}
			len = INTERFACE_CreateMessage16(msgBuf, instruction, val1, val2);
			INTERFACE_SendMessage(msgBuf, len);
		}
		len = INTERFACE_CreateMessage16(msgBuf, instruction, 362, 362);
		INTERFACE_SendMessage(msgBuf, len);
		recordmode = RECORD_RPM;
		recordDone = false;
		INTERFACE_ResetPeriodics();
		enableIRQ();
	}
}

/*
 * @brief Callback for host data processing
 * @param dat Received data
 */
void INTERFACE_Process(INTERFACE_Data_t* dat)
{
	disableIRQ();
	switch(dat->instruction)
	{
	case ROBOT_INSTRUCTION_DUTYCYCLE:
		RPMCTRL_Ignore(&ctrlLeft, true, &piLeft);
		RPMCTRL_Ignore(&ctrlRight, true, &piRight);
		RPMCTRL_SetDest(&ctrlLeft, (int)((short)dat->val1), &piLeft);
		RPMCTRL_SetDest(&ctrlRight, (int)((short)dat->val2), &piRight);
		break;
	case ROBOT_INSTRUCTION_RPM:
		RPMCTRL_Ignore(&ctrlLeft, false, &piLeft);
		RPMCTRL_Ignore(&ctrlRight, false, &piRight);
		RPMCTRL_SetDest(&ctrlLeft, (int)((short)dat->val1), &piLeft);
		RPMCTRL_SetDest(&ctrlRight, (int)((short)dat->val2), &piRight);
		break;
	case ROBOT_INSTRUCTION_LED:
		HAL_GPIO_WritePin(LED_GPIO_Port, LED_Pin, (GPIO_PinState)dat->val2);
		break;
	case ROBOT_INSTRUCTION_RECORDRPM:
		recordmode = RECORD_RPM;
		RPMCTRL_StartRecord(&ctrlLeft, (uint32_t)dat->val1, &record1, false);
		RPMCTRL_StartRecord(&ctrlRight, (uint32_t)dat->val2, &record2, false);
		break;
	case ROBOT_INSTRUCTION_RECORDCURRENT:
		recordmode = RECORD_CURRENT;
		RPMCTRL_StartRecord(&ctrlLeft, (uint32_t)dat->val1, &record1, true);
		RPMCTRL_StartRecord(&ctrlRight, (uint32_t)dat->val2, &record2, true);
		break;
	case ROBOT_INSTRUCTION_LEFT_KP:
		CTRL_Init(piLeft.Ka, float_2x16(dat->val1, dat->val2), piLeft.Tn, piLeft.Td, piLeft.T, piLeft.Lp, piLeft.maxIn, piLeft.maxOut, &piLeft);
		break;
	case ROBOT_INSTRUCTION_LEFT_TN:
		CTRL_Init(piLeft.Ka, piLeft.Kp, float_2x16(dat->val1, dat->val2), piLeft.Td, piLeft.T, piLeft.Lp, piLeft.maxIn, piLeft.maxOut, &piLeft);
		break;
	case ROBOT_INSTRUCTION_LEFT_TD:
		CTRL_Init(piLeft.Ka, piLeft.Kp, piLeft.Tn, float_2x16(dat->val1, dat->val2), piLeft.T, piLeft.Lp, piLeft.maxIn, piLeft.maxOut, &piLeft);
		break;
	case ROBOT_INSTRUCTION_LEFT_KA:
		CTRL_Init(float_2x16(dat->val1, dat->val2), piLeft.Kp, piLeft.Tn, piLeft.Td, piLeft.T, piLeft.Lp, piLeft.maxIn, piLeft.maxOut, &piLeft);
		break;
	case ROBOT_INSTRUCTION_RIGHT_KP:
		CTRL_Init(piRight.Ka, float_2x16(dat->val1, dat->val2), piRight.Tn, piRight.Td, piRight.T, piRight.Lp, piRight.maxIn, piRight.maxOut, &piRight);
		break;
	case ROBOT_INSTRUCTION_RIGHT_TN:
		CTRL_Init(piRight.Ka, piRight.Kp, float_2x16(dat->val1, dat->val2), piRight.Td, piRight.T, piRight.Lp, piRight.maxIn, piRight.maxOut, &piRight);
		break;
	case ROBOT_INSTRUCTION_RIGHT_TD:
		CTRL_Init(piRight.Ka, piRight.Kp, piRight.Tn, float_2x16(dat->val1, dat->val2), piRight.T, piRight.Lp, piRight.maxIn, piRight.maxOut, &piRight);
		break;
	case ROBOT_INSTRUCTION_RIGHT_KA:
		CTRL_Init(float_2x16(dat->val1, dat->val2), piRight.Kp, piRight.Tn, piRight.Td, piRight.T, piRight.Lp, piRight.maxIn, piRight.maxOut, &piRight);
		break;
	case ROBOT_INSTRUCTION_RPM_LOWPASS:
		CTRL_Init(piLeft.Ka, piLeft.Kp, piLeft.Tn, piLeft.Td, piLeft.T, float_2x16(dat->val1, dat->val2), piLeft.maxIn, piLeft.maxOut, &piLeft);
		CTRL_Init(piRight.Ka, piRight.Kp, piRight.Tn, piRight.Td, piRight.T, float_2x16(dat->val1, dat->val2), piRight.maxIn, piRight.maxOut, &piRight);
		break;
	case ROBOT_INSTRUCTION_RECORDHEADING:
		records = uint32_2x16(dat->val1, dat->val2);
		recordDone = false;
		recordIt = 0;
		QUEUE_Reset(&record1);
		QUEUE_Reset(&record2);
		recordmode = RECORD_HEADING;
		break;
	case ROBOT_PERIODIC_DATE:
	case ROBOT_PERIODIC_ENCODERS:
	case ROBOT_PERIODIC_HEADING:
	case ROBOT_PERIODIC_LATLON:
	case ROBOT_PERIODIC_TIME:
		INTERFACE_SetPeriod((uint8_t)dat->instruction, dat->val2);
		break;
	case ROBOT_INSTRUCTION_TERMINALMODE:
		TERMINALMODE_Config(&terminalMode, dat->val2);
		INTERFACE_EnableCRC(!(TERMINAL_NOCS == terminalMode.input));
	case ROBOT_INSTRUCTION_LEFT_CORRFAC_SHORT:
		ctrlLeft.corrfacShort = float_2x16(dat->val1, dat->val2);
		break;
	case ROBOT_INSTRUCTION_LEFT_CORRFAC_LONG:
		ctrlLeft.corrfacLong = float_2x16(dat->val1, dat->val2);
		break;
	case ROBOT_INSTRUCTION_RIGHT_CORRFAC_SHORT:
		ctrlRight.corrfacShort = float_2x16(dat->val1, dat->val2);
		break;
	case ROBOT_INSTRUCTION_RIGHT_CORRFAC_LONG:
		ctrlRight.corrfacLong = float_2x16(dat->val1, dat->val2);
		break;
	case ROBOT_INSTRUCTION_RESET:
		ctrlLeft.eternalTicks = 0;
		ctrlRight.eternalTicks = 0;
		break;
	case ROBOT_INSTRUCTION_BALLSHIT:
		shit = true;
		break;
	default: break;
	}
	enableIRQ();
}

/*
 * @brief Get Systick with 100 us resolution.
 * @brief Can overflow.
 * @return Time in us
 */
uint32_t getTick()
{
	return htim2.Instance->CNT * 100;
}

/**
 * @brief Interrupt for first encoder
 */
void ISR_ENCODER1(void)
{
	disableIRQ();
	static bool isLow = false;
	static uint32_t tick = 0;
	tick = getTick();
	isLow = !(GPIO_PIN_SET == HAL_GPIO_ReadPin(ENCODER1_GPIO_Port, ENCODER1_Pin));
	RPMCTRL_Tick(&ctrlLeft, tick, isLow);
	ODOMETRY_Update(&odom, ctrlLeft.rpm, ctrlRight.rpm, tick);
	enableIRQ();
}

/*
 * @brief Interrupt for second encoder
 */
void ISR_ENCODER0(void)
{
	disableIRQ();
	static bool isLow = false;
	static uint32_t tick = 0;
	tick = getTick();
	isLow = !(GPIO_PIN_SET == HAL_GPIO_ReadPin(ENCODER0_GPIO_Port, ENCODER0_Pin));
	RPMCTRL_Tick(&ctrlRight, tick, isLow);
	ODOMETRY_Update(&odom, ctrlLeft.rpm, ctrlRight.rpm, tick);
	enableIRQ();
}

/*
 * @brief 10 Hz timer interrupt for control loops
 */
void ISR_10Hz(void)
{
	disableIRQ();
	HAL_GPIO_WritePin(CS_GPIO_Port, CS_Pin, 1);
	RPMCTRL_Update(&ctrlLeft, &piLeft);
	RPMCTRL_Update(&ctrlRight, &piRight);
	Powertrain_SetDutycycles(ctrlLeft.dutyCycle, ctrlRight.dutyCycle);
	ADCFILTER_Process(adcValues, ADC_SAMPLES);
	RPMCTRL_SetAvgTorque(&ctrlLeft, (uint16_t)ADCFILTER_Values[ADC_IS12]);
	RPMCTRL_SetAvgTorque(&ctrlRight, (uint16_t)ADCFILTER_Values[ADC_IS34]);
	HAL_ADC_Start_DMA(&hadc1, adcValues, ADC_SAMPLES);
	HAL_GPIO_WritePin(CS_GPIO_Port, CS_Pin, 0);
	enableIRQ();
}

/*
 * @brief Emergency button event
 */
void ISR_EMSTOP(void)
{
	static bool isLow = false;
	isLow = (GPIO_PIN_SET == HAL_GPIO_ReadPin(EMSTOP_GPIO_Port, EMSTOP_Pin));

	emergencyStop.isEvent = true;
	emergencyStop.isEmergency = isLow;

	Powertrain_SetDutycycles(0, 0);
	RPMCTRL_SetDest(&ctrlLeft, 0, &piLeft);
	RPMCTRL_SetDest(&ctrlRight, 0, &piRight);
}

/*
 * @brief NMEA HDT data callback from compass
 * @param dat HDT data
 */
void NMEA_CallbackHDT(NMEA_HDTData_t* dat)
{
	MOVINGAVG_AddSample(&kvhFilter, (int)dat->heading);
	MOVINGAVG_Calculate(&kvhFilter);
	if(kvhFilter.output > 180)
	{
		kvhFilter.output -= 360;
	}

	if(RECORD_HEADING == recordmode)
	{
		if(recordIt < records)
		{
			if(!QUEUE_IsFull(&record1))
			{
				QUEUE_Push16((uint16_t)kvhFilter.output, &record1);
			}
			else if(!QUEUE_IsFull(&record2))
			{
				QUEUE_Push16((uint16_t)kvhFilter.output, &record2);
			}
			recordIt ++;
		}
		else
		{
			recordDone = true;
		}
	}
}

/*
 * @brief NMEA RMC data callback from GPS
 * @param dat RMC data
 */
void NMEA_CallbackRMC(NMEA_RMCData_t* dat)
{
	gpsData.latitude = dat->latitude;
	gpsData.longitude = dat->longitude;
	gpsData.day = dat->day;
	gpsData.month = dat->month;
	gpsData.year = dat->year;
	gpsData.hours = dat->hours;
	gpsData.minutes = dat->minutes;
	gpsData.seconds = dat->seconds;
}

void ISR_DMA(void){}
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
int main(void)
{
  /* MCU Configuration--------------------------------------------------------*/

  /* Reset of all peripherals, Initializes the Flash interface and the Systick. */
  HAL_Init();

  /* Configure the system clock */
  SystemClock_Config();

  /* USER CODE BEGIN SysInit */
  // Init recording
  QUEUE_Init(&record1, recordBuf1, MEMDEPTH_RECORD);
  QUEUE_Init(&record2, recordBuf2, MEMDEPTH_RECORD);

  // Init host communication
  QUEUE_Init(&interfaceQueue, interfaceBuf, MEMDEPTH_INTERFACE);
  INTERFACE_Init();
  INTERFACE_AddPeriodic(ROBOT_PERIODIC_LATLON, ROBOT_PERIOD_LATLON);
  INTERFACE_AddPeriodic(ROBOT_PERIODIC_TIME, ROBOT_PERIOD_TIME);
  INTERFACE_AddPeriodic(ROBOT_PERIODIC_DATE, ROBOT_PERIOD_DATE);
  INTERFACE_AddPeriodic(ROBOT_PERIODIC_HEADING, ROBOT_PERIOD_HEADING);
  INTERFACE_AddPeriodic(ROBOT_PERIODIC_ENCODERS, ROBOT_PERIOD_ENCODERS);
  INTERFACE_AddPeriodic(ROBOT_PERIODIC_ODOM, ROBOT_PERIOD_ODOM);

  // Init RPM control
  CTRL_Init(ROBOT_LEFT_KA, ROBOT_LEFT_KP, ROBOT_LEFT_TN, ROBOT_LEFT_TD, ROBOT_RPMCTRL_T, ROBOT_LEFT_LP, ROBOT_RPM_MAX, ROBOT_DUTYCYCLE_MAX, &piLeft);
  CTRL_Init(ROBOT_RIGHT_KA, ROBOT_RIGHT_KP, ROBOT_RIGHT_TN, ROBOT_RIGHT_TD, ROBOT_RPMCTRL_T, ROBOT_RIGHT_LP, ROBOT_RPM_MAX, ROBOT_DUTYCYCLE_MAX, &piRight);
  RPMCTRL_Init(ROBOT_ENCODER_STEPS, ROBOT_LEFT_CORRFACSHORT, ROBOT_LEFT_CORRFACLONG, &ctrlLeft);
  RPMCTRL_Init(ROBOT_ENCODER_STEPS, ROBOT_RIGHT_CORRFACSHORT, ROBOT_RIGHT_CORRFACLONG, &ctrlRight);
  ODOMETRY_Init(ROBOT_ENCODER_STEPS, ROBOT_WHEELRADIUS_M, ROBOT_WHEELWIDTH_M, &odom);

  // Init UART sensors
  QUEUE_Init(&kvhQueue, kvhBuf, MEMDEPTH_KVH);
  QUEUE_Init(&gpsQueue, gpsBuf, MEMDEPTH_GPS);

  MOVINGAVG_Init(&kvhFilter, kvhFilterBuf, MEMDEPTH_KVH_MOVINGAVG);
  NMEA_Init(&kvhInput);

  NMEA_Init(&gpsInput);

  TERMINALMODE_Config(&terminalMode, TERMINAL_DISABLE);

  emergencyStop.isEmergency = false;
  emergencyStop.isEvent = false;
  __enable_irq();

  /* USER CODE END SysInit */

  /* Initialize all configured peripherals */
  MX_GPIO_Init();
  MX_DMA_Init();
  MX_ADC1_Init();
  MX_TIM1_Init();
  MX_TIM2_Init();
  MX_TIM3_Init();
  MX_TIM4_Init();
  MX_USART1_UART_Init();
  MX_USART2_UART_Init();
  MX_USART3_UART_Init();
  /* USER CODE BEGIN 2 */

  Powertrain_Init();
  Ballshitter_Init();
  //KVH_Init();

  // Init software I2C
  QUEUE_Init(&wireRxQueue, (char*)wireRx, 20);
  QUEUE_Init(&wireTxQueue, (char*)wireTx, 20);
  WIRE_Init(&wire,
		  SDA_GPIO_Port, SDA_Pin,
		  SCL_GPIO_Port, SCL_Pin,
		  400,
		  &wireRxQueue, &wireTxQueue);
  WIRE_Begin(&wire);

  /* USER CODE END 2 */

  /* Infinite loop */
  /* USER CODE BEGIN WHILE */
  while (1)
  {
//	  disableIRQ();
//	  __disable_irq();
	  INTERFACE_Parse(&interfaceQueue);
	  RECORD_Process();
	  INTERFACE_ProcessPeriodics();
	  TERMINAL_Process();
	  KVH_Process();
//	  GPS_Process();
	  EMERGENCY_Process();
	  Ballshitter_Drop();
//	  	__enable_irq();

//	  	HAL_UART_Receive_IT(&huart1, (uint8_t*)&uart1In, 1);
//	  	HAL_UART_Receive_IT(&huart2, (uint8_t*)&uart2In, 1);
//	  	HAL_UART_Receive_IT(&huart3, (uint8_t*)&uart3In, 1);
//	    HAL_TIM_Base_Start_IT(&htim2);
//	    HAL_TIM_PWM_Start(&htim3, TIM_CHANNEL_1);
//	    HAL_TIM_PWM_Start(&htim3, TIM_CHANNEL_2);
//	    HAL_TIM_PWM_Start(&htim3, TIM_CHANNEL_3);
//	    HAL_TIM_PWM_Start(&htim3, TIM_CHANNEL_4);
//	    HAL_TIM_Base_Start_IT(&htim4);
//	  HAL_Delay(200);
//	  enableIRQ();
    /* USER CODE END WHILE */

    /* USER CODE BEGIN 3 */
  }
  /* USER CODE END 3 */
}

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
/* USER CODE BEGIN 4 */
/*
 * @brief Init powertrain.
 */
void Powertrain_Init()
{
	Powertrain_EnableMotors(1);
	Powertrain_SetDutycycles(0, 0);
}

/*
 * @brief Enable motors
 * @param enableState true for enabling
 */
void Powertrain_EnableMotors(int enableState)
{
	HAL_GPIO_WritePin(INH12_GPIO_Port, INH12_Pin, enableState);
	HAL_GPIO_WritePin(INH34_GPIO_Port, INH34_Pin, enableState);
}

/*
 * @brief Set motor dutycycles
 * @param left dutycycle from -100 to 100
 * @param right dutycycle from -100 to 100
 */
void Powertrain_SetDutycycles(int left, int right)
{
	static int lastLeft = 0;
	static int lastRight = 0;

	if(left > 100)
	{
		left = 100;
	}
	if(left < -100)
	{
		left = -100;
	}

	if(right > 100)
	{
		right = 100;
	}
	if(right < -100)
	{
		right = -100;
	}

	left *= 10;
	right *= 10;

//	if(left != lastLeft)
//	{
		if(left < 0)
		{
			left = -left;
			htim3.Instance->CCR3 = left;
			htim3.Instance->CCR4 = 0;
		}
		else
		{
			htim3.Instance->CCR3 = 0;
			htim3.Instance->CCR4 = left;
		}
		lastLeft = left;
//	}

//	if(right != lastRight)
//	{
		if(right < 0)
		{
			right = -right;
			htim3.Instance->CCR1 = right;
			htim3.Instance->CCR2 = 0;
		}
		else
		{
			htim3.Instance->CCR1 = 0;
			htim3.Instance->CCR2 = right;
		}
//		lastRight = right;
//	}
}

void Servo_Set(int angle)
{
	if(angle < 0) angle = 0;
	else if(angle > 180) angle = 180;

	htim1.Instance->CCR1 = SERVO_OFFSET + (angle * SERVO_RANGE) / 180;
}

void Ballshitter_Init()
{
	shit = false;
	Servo_Set(180);
	HAL_Delay(BALLSHITTER_TIME);
}

void Ballshitter_Drop()
{
	static uint32_t time = 0;
	static bool init = false;
	uint32_t current = HAL_GetTick();
	if(!shit || !init)
	{
		init = true;
		time = HAL_GetTick();
	}
	else if(shit)
	{
		uint32_t delta = current - time;
		if(delta < BALLSHITTER_TIME)
		{
			Servo_Set(180 - (180 * delta) / BALLSHITTER_TIME);
		}
		else if(delta < 2 * BALLSHITTER_TIME)
		{
			Servo_Set((180 * (delta - BALLSHITTER_TIME)) / BALLSHITTER_TIME);
		}
		shit = delta < 3 * BALLSHITTER_TIME;
	}
}

/*
 * @brief Init KVH-C100 compass.
 */
void KVH_Init()
{

	  char kvhConfigNmeaStr[5] = { '=', 't' , ',', '0', '\r' }; // NMEA protocol
	  char kvhConfigSpeedStr[8] = { '=', 'r', ',' , '6' , '0', '0', '\r' }; // 1Hz
	  char kvhConfigUnitStr[5] = { '=', 'i' , ',', 'd', '\r' }; // degrees as unit
	  char kvhDampingTypeStr[7] = { '=',  'd', 't', '0', ',', '3', '\r' }; // double IIR
	  char kvhDampingTimeStr[6] = { '=',  'd', '0', ',', '9', '\r' }; // 24 secs
	  char kvhInitStr[3] = { 's', '\r' }; // start

	  HAL_UART_Transmit(&huart2, (uint8_t*)kvhConfigNmeaStr, 5, 1000);
	  HAL_Delay(200);
	  HAL_UART_Transmit(&huart2, (uint8_t*)kvhConfigUnitStr, 5, 1000);
	  HAL_Delay(200);
	  HAL_UART_Transmit(&huart2, (uint8_t*)kvhConfigSpeedStr, 7, 1000);
	  HAL_Delay(200);
	  HAL_UART_Transmit(&huart2, (uint8_t*)kvhDampingTypeStr, 7, 1000);
	  HAL_Delay(200);
	  HAL_UART_Transmit(&huart2, (uint8_t*)kvhDampingTimeStr, 6, 1000);
	  HAL_Delay(200);
	  HAL_UART_Transmit(&huart2, (uint8_t*)kvhInitStr, 2, 1000);
	  HAL_Delay(200);
}

/* USER CODE END 4 */
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


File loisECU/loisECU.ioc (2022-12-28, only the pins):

Mcu.UserName=STM32F103C8Tx
PA6.GPIO_Label=BATSENSE
PB0.GPIO_Label=PWM2
PB6.GPIO_Label=SCL
PB11.Signal=USART3_RX
PC15-OSC32_OUT.GPIO_Label=INH34
PD1-OSC_OUT.Signal=RCC_OSC_OUT
PA15.GPIO_Label=ENCODER1
PB6.Signal=GPIO_Output
PB12.GPIO_Label=EMSTOP
PB1.GPIO_Label=PWM1
PB7.Signal=GPIO_Output
PA8.Signal=S_TIM1_CH1
PB7.GPIO_Label=SDA
PB1.Signal=S_TIM3_CH4
PA6.Signal=ADCx_IN6
PA10.Signal=USART1_RX
PA15.Signal=GPXTI15
PB5.GPIO_Label=PWM4
PC14-OSC32_IN.GPIO_Label=INH12
PA4.GPIO_Label=IS12
PB4.Signal=S_TIM3_CH1
PA3.Signal=USART2_RX
PB3.GPIO_Label=ENCODER0
PC13-TAMPER-RTC.Signal=GPIO_Output
PD0-OSC_IN.Signal=RCC_OSC_IN
PC14-OSC32_IN.Signal=GPIO_Output
PA0-WKUP.GPIO_Label=BEMF12
PA0-WKUP.Signal=ADCx_IN0
PA13.Signal=SYS_JTMS-SWDIO
PA8.GPIO_Label=SERVO
PA9.Signal=USART1_TX
PC15-OSC32_OUT.Signal=GPIO_Output
PA1.Signal=ADCx_IN1
PB10.Signal=USART3_TX
PA5.Signal=ADCx_IN5
PC13-TAMPER-RTC.GPIO_Label=LED
PB4.GPIO_Label=PWM3
PA1.GPIO_Label=BEMF34
PA2.Signal=USART2_TX
PB3.Signal=GPXTI3
PA4.Signal=ADCx_IN4
PB5.Signal=S_TIM3_CH2
PA7.GPIO_Label=CS
PA5.GPIO_Label=IS34
PA11.Signal=USB_DM
PA14.Signal=SYS_JTCK-SWCLK
PB0.Signal=S_TIM3_CH3
PB12.Signal=GPXTI12
PA7.Signal=GPIO_Output

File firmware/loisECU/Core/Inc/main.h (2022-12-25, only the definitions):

#define LED_Pin GPIO_PIN_13
#define LED_GPIO_Port GPIOC
#define INH12_Pin GPIO_PIN_14
#define INH12_GPIO_Port GPIOC
#define INH34_Pin GPIO_PIN_15
#define INH34_GPIO_Port GPIOC
#define BEMF12_Pin GPIO_PIN_0
#define BEMF12_GPIO_Port GPIOA
#define BEMF34_Pin GPIO_PIN_1
#define BEMF34_GPIO_Port GPIOA
#define IS12_Pin GPIO_PIN_4
#define IS12_GPIO_Port GPIOA
#define IS34_Pin GPIO_PIN_5
#define IS34_GPIO_Port GPIOA
#define BATSENSE_Pin GPIO_PIN_6
#define BATSENSE_GPIO_Port GPIOA
#define CS_Pin GPIO_PIN_7
#define CS_GPIO_Port GPIOA
#define PWM2_Pin GPIO_PIN_0
#define PWM2_GPIO_Port GPIOB
#define PWM1_Pin GPIO_PIN_1
#define PWM1_GPIO_Port GPIOB
#define EMSTOP_Pin GPIO_PIN_12
#define EMSTOP_GPIO_Port GPIOB
#define EMSTOP_EXTI_IRQn EXTI15_10_IRQn
#define SERVO_Pin GPIO_PIN_8
#define SERVO_GPIO_Port GPIOA
#define ENCODER1_Pin GPIO_PIN_15
#define ENCODER1_GPIO_Port GPIOA
#define ENCODER1_EXTI_IRQn EXTI15_10_IRQn
#define ENCODER0_Pin GPIO_PIN_3
#define ENCODER0_GPIO_Port GPIOB
#define ENCODER0_EXTI_IRQn EXTI3_IRQn
#define PWM3_Pin GPIO_PIN_4
#define PWM3_GPIO_Port GPIOB
#define PWM4_Pin GPIO_PIN_5
#define PWM4_GPIO_Port GPIOB
#define SCL_Pin GPIO_PIN_6
#define SCL_GPIO_Port GPIOB
#define SDA_Pin GPIO_PIN_7
#define SDA_GPIO_Port GPIOB

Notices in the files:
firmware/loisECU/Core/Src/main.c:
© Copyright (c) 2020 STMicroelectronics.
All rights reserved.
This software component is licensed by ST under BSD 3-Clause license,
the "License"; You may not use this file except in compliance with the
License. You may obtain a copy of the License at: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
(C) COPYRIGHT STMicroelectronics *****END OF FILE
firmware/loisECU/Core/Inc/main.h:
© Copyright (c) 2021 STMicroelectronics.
